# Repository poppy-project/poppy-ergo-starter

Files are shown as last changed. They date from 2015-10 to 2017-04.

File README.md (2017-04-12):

# Poppy Ergo Starter



Poppy Ergo Starter robot is a small and low cost 4-degree-of-freedom robot arm. It consists of very simple shapes which can be easily 3D printed with FDM printers and laser cutted.

It works with Dynamixel XL-320 motors, and a Raspberry Pi for control.

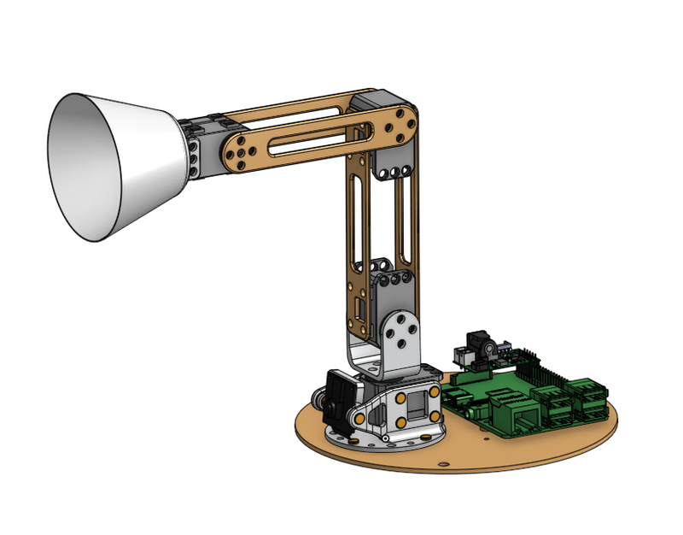
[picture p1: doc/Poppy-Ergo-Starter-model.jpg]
PoppyErgoStarter


It comes with three tools:
* a lampshade
* a grasper
* a pen holder

The Poppy Ergo Starter is ideal to start manipulating robots and learn robotic without difficulties.

It is particularly well suited for educational purposes (cheap, simple to assemble, and easily controllable) or can be a very nice desk decoration for geeks and makers...

## Contributing

You can share your experience, new design, ideas or questions on the [Poppy project forum](https://forum.poppy-project.org/).

To contribute to this repository, you can [fork it](https://help.github.com/articles/fork-a-repo/) and propose a [pull request](https://help.github.com/articles/using-pull-requests/) *([Another useful link](https://gun.io/blog/how-to-github-fork-branch-and-pull-request/))*

## License

All the technological development work made in the Poppy project is freely available under open source licenses. Only the name usage *"Poppy"* is restricted and protected as an international trademark, please contact us if you want to use it or have more information.

| License | Hardware | Software |
| --- | :---: | :---: |
| Title  | [Creative Commons BY-SA](http://creativecommons.org/licenses/by-sa/4.0/)  |[GPL v3](http://www.gnu.org/licenses/gpl.html)  |
| Logo  |   |GPL V3 (http://www.gnu.org/licenses/gpl.html)  |

## The Poppy project history

The Poppy project was born in 2012 in the [Flowers laboratory](https://flowers.inria.fr/) at [Inria Bordeaux Sud-Ouest](http://www.inria.fr/en/centre/bordeaux).
It was initiated during [Matthieu Lapeyre](https://github.com/matthieu-lapeyre)'s PhD Thesis surpervised by [Pierre Yves Oudeyer](http://www.pyoudeyer.com/). At the beginning, the development team was composed by [Matthieu Lapeyre](https://github.com/matthieu-lapeyre) (mechanics & design), [Pierre Rouanet](https://github.com/pierre-rouanet) (software) and [Jonathan Grizou](http://jgrizou.com/) (electronics).

This project is initially a fundamental research project financed by [ERC Grant Explorer](http://erc.europa.eu/) to explore the role of embodiement and morphology properties on cognition and especially on the learning of sensori-motor tasks.

## More on the project

- [Website](https://www.poppy-project.org)
- [Forum](https://forum.poppy-project.org)
- [Youtube](https://www.youtube.com/channel/UC3iVGSr-vMgnFlIfPBH2p7Q)
- [Twitter](https://twitter.com/poppy_project)
- [Flickr](https://www.flickr.com/photos/poppy-project)
- [Vimeo](https://vimeo.com/poppyproject)
- [Thingiverse](http://www.thingiverse.com/poppy_project/)

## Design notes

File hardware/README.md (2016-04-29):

## Onshape version
The up to date hardware version is made with [Onshape](https://www.onshape.com/), which is a proprietary online CAD software, free to use for public projects.

You can view and modify the hardware parts on Onshape ([link of the onshape project](https://cad.onshape.com/documents/57024ba6e4b0bd431e251b54/v/f9f9475a8e982b501b19085f/e/ed40471c06b378f3c094c206)), but an account (free) is required.

## OpenScad version
Poppy Ergo Starter was originally made by Jonathan Grizou (@jgrizou) with [OpenScad](http://www.openscad.org/).
This was inspired by the [Metabot project](https://github.com/Rhoban/Metabot/).

The OpenScad version of hardware is kept [here](https://github.com/poppy-project/poppy-ergo-starter/tree/OpenSCAD) for memory and educational example of an OpenScad project, but it is __no longer maintained__.

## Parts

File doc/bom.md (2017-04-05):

# Bill of materials

Here you will find the complete list of material (BOM) needed to build a Poppy Ergo Starter.

## Poppy's material

- 1x [Pixl board](https://github.com/poppy-project/pixl) *(electronic board to control XL320 motors)*
- 1x [disk_support.stl](https://github.com/poppy-project/poppy-ergo-starter/blob/master/hardware/STL/disk_support.stl) (using laser cutting) the 2D plan can be found [here](https://github.com/poppy-project/poppy-ergo-starter/tree/master/hardware/disk_support). *You can also 3D print the base but it will take a lot of time*
- 2x [4dof-parts](https://github.com/poppy-project/poppy-ergo-starter/tree/master/hardware/4dof-parts.pdf) by laser cutting
- the 3D printed parts [STL here](https://github.com/poppy-project/poppy-ergo-starter/tree/master/hardware/STL)
  - 1x [base.stl](https://github.com/poppy-project/poppy-ergo-starter/blob/master/hardware/STL/base.stl)
  - 1x [long_U.stl](https://github.com/poppy-project/poppy-ergo-starter/blob/master/hardware/STL/long_U.stl)
  - 1x [short_U.stl](https://github.com/poppy-project/poppy-ergo-starter/blob/master/hardware/STL/short_U.stl)
  - 1x [support_camera.stl](https://github.com/poppy-project/poppy-ergo-starter/blob/master/hardware/STL/long_U.stl)
  - the different tools
    - 1x [lamp.stl](https://github.com/poppy-project/poppy-ergo-starter/blob/master/hardware/STL/tools/lamp.stl)
    - 1x [gripper-fixation.stl](https://github.com/poppy-project/poppy-ergo-starter/blob/master/hardware/STL/tools/gripper-fixation.stl)
    - 1x [gripper-fixed_part.stl](https://github.com/poppy-project/poppy-ergo-starter/blob/master/hardware/STL/tools/gripper-fixed_part.stl)
    - 1x [gripper-rotative_part.stl](https://github.com/poppy-project/poppy-ergo-starter/blob/master/hardware/STL/tools/gripper-rotative_part.stl)
    - 1x [pen-holder.stl](https://github.com/poppy-project/poppy-ergo-starter/blob/master/hardware/STL/tools/pen-holder.stl)
    - 1x [pen-screw.stl](https://github.com/poppy-project/poppy-ergo-starter/blob/master/hardware/STL/tools/pen-screw.stl)

## Robotis parts

- 4x Robotis dynamixel motors XL-320
- 1x set of OLLO rivets (about 50 colored and 1 grey)
- 1x OLLO TOOL

## Screw

- 4x M2.5x6mm screw (for fixing the Raspberry Pi on the base)
- 4x M2x5mm screw (for fixing the camera)
- 4x M2 nuts (fixing camera)
- 1x Standoff Male/Female M2.5 10mm

## Various electronics

- 1x Raspberry Pi 2 or Raspberry Pi 3
- 1x micro SD 8Go
- 1x Rasperry Pi camera
- 1x AC power 7.5V 2A with a 2.1 x 5.5 x 9.5 jack connector ([this one](http://fr.rs-online.com/web/p/alimentations-enfichables/7262814/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) for instance).
- Short ethernet cable

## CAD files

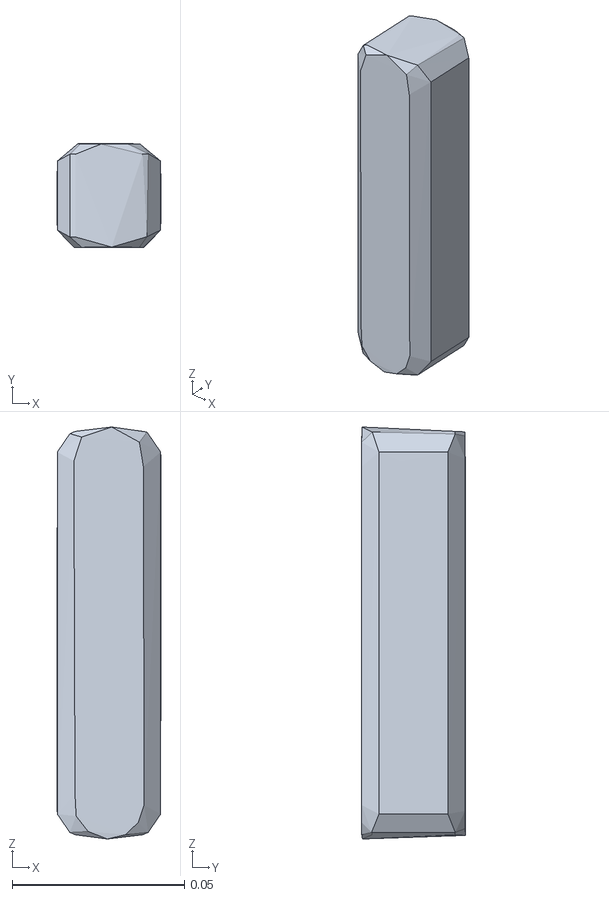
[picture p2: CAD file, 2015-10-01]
hardware/URDF/meshes/arm1_respondable.stl
0.0301 x 0.0301 x 0.119

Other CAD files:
hardware/STEP/tools/pen_holder.step
hardware/STEP/U_parts.step
hardware/STL/support_camera.stl
hardware/STL/tools/gripper-rotative_part.stl
hardware/URDF/meshes/base_motor_respondable.stl
hardware/STEP/base.step
hardware/STEP/tools/lamp.step
hardware/STL/4dofs-side2side.stl
hardware/STL/tools/gripper-fixation.stl
hardware/URDF/meshes/holder_visual.stl
hardware/STEP/tools/gripper.step
hardware/STL/short_U.stl
hardware/STL/tools/gripper-fixed_part.stl
hardware/URDF/meshes/holder_respondable.stl
hardware/STL/long_U.stl
hardware/URDF/meshes/base_motor_visual.stl
hardware/STL/4dofs-horn2horn.stl
hardware/STL/base.stl
hardware/STL/disk_support.stl
hardware/STL/tools/lamp.stl
hardware/STL/tools/pen-holder.stl
hardware/STL/tools/pen-screw.stl
hardware/URDF/meshes/U_horn_respondable.stl
hardware/URDF/meshes/U_horn_visual.stl
hardware/URDF/meshes/arm1_visual.stl
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

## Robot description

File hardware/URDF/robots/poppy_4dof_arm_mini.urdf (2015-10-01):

<?xml version="1.0" encoding="utf-8"?>
<robot name="Poppy_4dof_Arm_Mini">
	<link name="base_motor">
		<inertial>
			<origin xyz="0 -0.003349 -0.007144" rpy="0 0 0"></origin>
			<mass value="0.0391346684"></mass>
			<inertia ixx="0.01991511" ixy="-1.627E-12" ixz="-3.3502E-11" iyy="0.018856556" iyz="0.0010117547" izz="0.032481808"></inertia>
		</inertial>
		<visual>
			<origin xyz="0 0 0" rpy="0 0 0"></origin>
			<geometry>
				<mesh filename="package://meshes/base_motor_visual.STL"></mesh>
			</geometry>
			<material name="">
				<color rgba="0.9 0.9 0.9 1.0"></color>
			</material>
		</visual>
		<collision>
			<origin xyz="0 0 0" rpy="0 0 0"></origin>
			<geometry>
				<mesh filename="package://meshes/base_motor_respondable.STL"></mesh>
			</geometry>
		</collision>
		<mass>0.0391346684</mass>
	</link>
	<link name="U_horn">
		<inertial>
			<origin xyz="0 0.013288 0" rpy="0 0 0"></origin>
			<mass value="0.0042280066"></mass>
			<inertia ixx="0.0014620794" ixy="0" ixz="-8.78E-13" iyy="0.0011395926" iyz="0" izz="0.0006457789"></inertia>
		</inertial>
		<visual>
			<origin xyz="0 0 0" rpy="0 0 0"></origin>
			<geometry>
				<mesh filename="package://meshes/U_horn_visual.STL"></mesh>
			</geometry>
			<material name="">
				<color rgba="0.9 0.9 0.9 1.0"></color>
			</material>
		</visual>
		<collision>
			<origin xyz="0 0 0" rpy="0 0 0"></origin>
			<geometry>
				<mesh filename="package://meshes/U_horn_respondable.STL"></mesh>
			</geometry>
		</collision>
		<mass>0.0042280066</mass>
	</link>
	<link name="arm_1">
		<inertial>
			<origin xyz="0 0.000057479 0.049499928" rpy="0 0 0"></origin>
			<mass value="0.0430952766"></mass>
			<inertia ixx="0.08214364" ixy="2.97266E-10" ixz="5.81285E-10" iyy="0.083140664" iyz="-6.131977E-09" izz="0.0061720795"></inertia>
		</inertial>
		<visual>
			<origin xyz="0 0 0" rpy="1.5708 0 0"></origin>
			<geometry>
				<mesh filename="package://meshes/arm1_visual.STL"></mesh>
			</geometry>
			<material name="">
				<color rgba="0.9 0.9 0.9 1.0"></color>
			</material>
		</visual>
		<collision>
			<origin xyz="0 0 0" rpy="1.5708 0 0"></origin>
			<geometry>
				<mesh filename="package://meshes/arm1_respondable.STL"></mesh>
			</geometry>
		</collision>
		<mass>0.0430952766</mass>
	</link>
	<link name="arm_2">
		<inertial>
			<origin xyz="0 0.050999855 0" rpy="0 0 0"></origin>
			<mass value="0.010259289"></mass>
			<inertia ixx="0.014484899" ixy="0" ixz="-2.42E-13" iyy="0.004054289" iyz="1.06451E-10" izz="0.017657572"></inertia>
		</inertial>
		<visual>
			<origin xyz="0 0 0" rpy="0 1.5708 3.14160 "></origin>
			<geometry>
				<mesh filename="package://meshes/arm2_visual.STL"></mesh>
			</geometry>
			<material name="">
				<color rgba="0.9 0.9 0.9 1.0"></color>
			</material>
		</visual>
		<collision>
			<origin xyz="0 0 0" rpy="0 1.57080 3.14160"></origin>
			<geometry>
				<mesh filename="package://meshes/arm2_respondable.STL"></mesh>
			</geometry>
		</collision>
		<mass>0.010259289</mass>
	</link>
	<link name="holder">
		<inertial>
			<origin xyz="0 -0.012510048 -0.000058315" rpy="0 0 0"></origin>
			<mass value="0.0212559855"></mass>
			<inertia ixx="0.0063271895" ixy="-1.9672E-11" ixz="-1.6458E-11" iyy="0.0024594695" iyz="1.7191568359E-05" izz="0.0058998525"></inertia>
		</inertial>
		<visual>
			<origin xyz="0 0 0" rpy="0 0 0 "></origin>
			<geometry>
				<mesh filename="package://meshes/holder_visual.STL"></mesh>
			</geometry>
			<material name="">
				<color rgba="0.9 0.9 0.9 1.0"></color>
			</material>
		</visual>
		<collision>
			<origin xyz="0 0 0" rpy="0 0 0"></origin>
			<geometry>
				<mesh filename="package://meshes/holder_respondable.STL"></mesh>
			</geometry>
		</collision>
		<mass>0.0212559855</mass>
	</link>
	<joint name="M1" type="revolute">
		<origin xyz="0 0 0.04" rpy="-1.5708 0 0"></origin>
		<parent link="base_motor"></parent>
		<child link="U_horn"></child>
		<axis xyz="0 1 0"></axis>
		<limit lower="-2.617993875" upper="2.617993875" effort="3.1" velocity="7.0"></limit>
	</joint>
	<joint name="M2" type="revolute">
		<origin xyz="0 0 0" rpy="0 0 0"></origin>
		<parent link="U_horn"></parent>
		<child link="arm_1"></child>
		<axis xyz="0 0 1"></axis>
		<limit lower="-1.5708" upper="1.5708" effort="3.1" velocity="7.0"></limit>
	</joint>
	<joint name="M3" type="revolute">
		<origin xyz="0 -0.099 0" rpy="0 0 0"></origin>
		<parent link="arm_1"></parent>
		<child link="arm_2"></child>
		<axis xyz="0 0 1"></axis>
		<limit lower="-2.617993875" upper="2.617993875" effort="3.1" velocity="7.0"></limit>
	</joint>
	<joint name="M4" type="revolute">
		<origin xyz="0 -0.099 0" rpy="0 0 0"></origin>
		<parent link="arm_2"></parent>
		<child link="holder"></child>
		<axis xyz="0 0 0"></axis>
		<limit lower="-2.617993875" upper="2.617993875" effort="3.1" velocity="7.0"></limit>
	</joint>
</robot>

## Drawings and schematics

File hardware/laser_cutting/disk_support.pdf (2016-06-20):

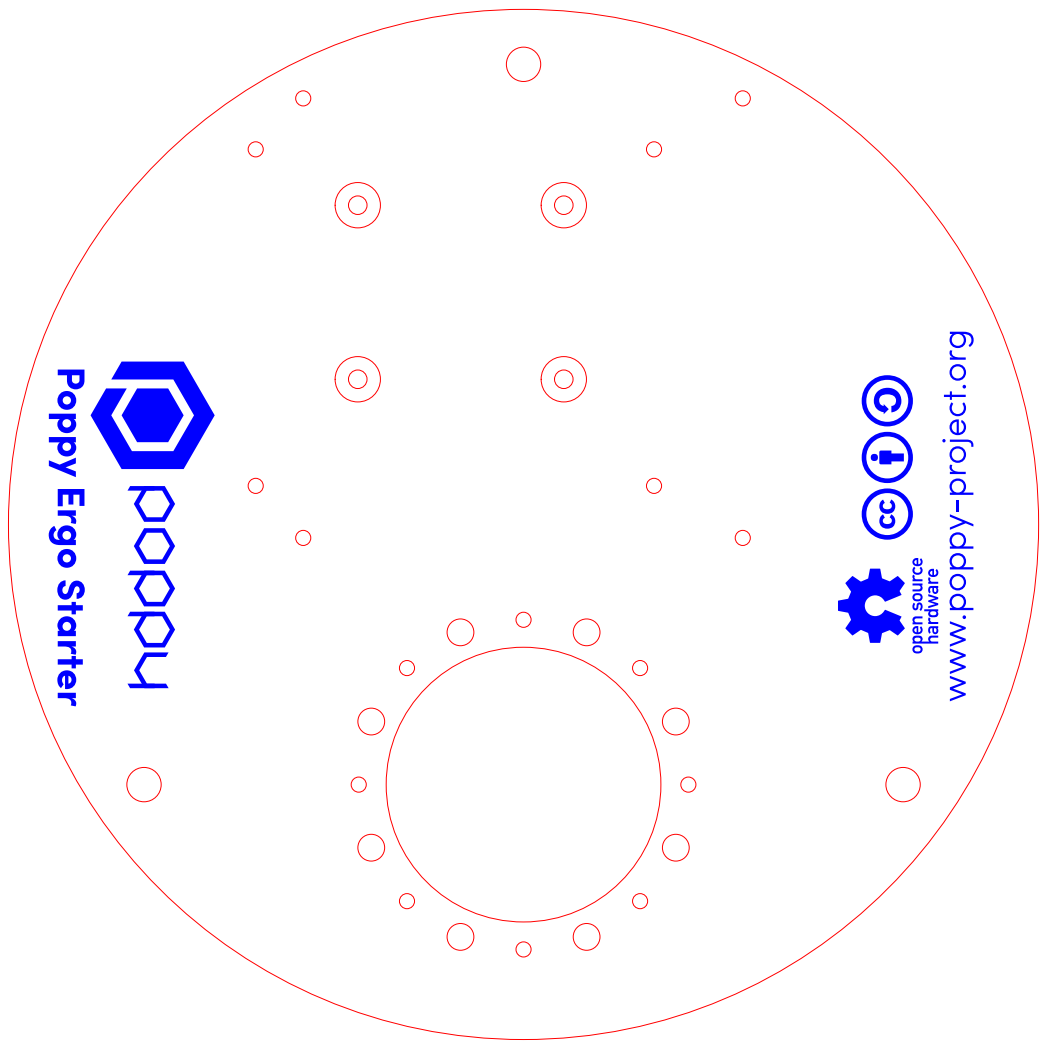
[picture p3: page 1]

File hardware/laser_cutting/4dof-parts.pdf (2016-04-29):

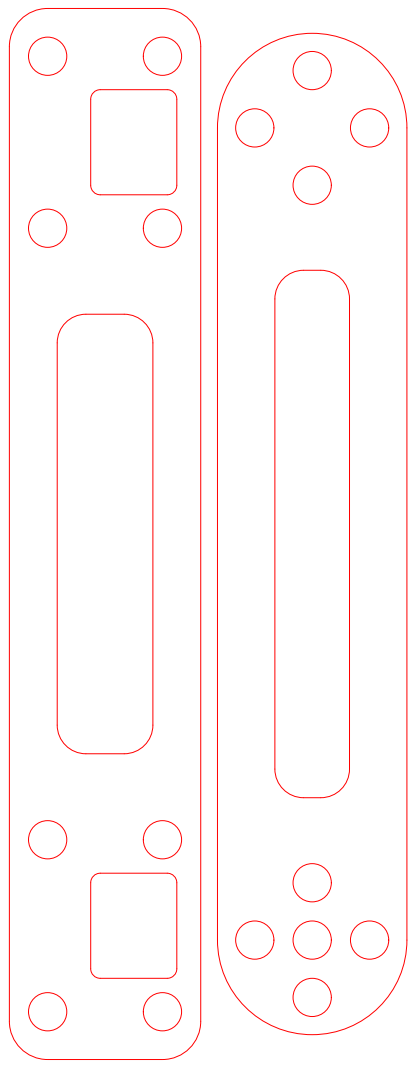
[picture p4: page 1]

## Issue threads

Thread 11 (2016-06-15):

Laser cutting

jjehl, 2016-06-15:
Cuttings for brace are missing in the pdf file.
It could be better to put diameter hole to 4 mm and not 4.1 because the laser has 0.2mm wide (to much clearance).

How did you process to make the PDF file for laser cutting from the onshape drawing ? I can update the doc. with the cutting for the brace.

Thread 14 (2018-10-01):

Usage with Snap!

celbertin, 2018-10-01:
Hi! I just installed Poppy Ergo Starter using:

> curl -L https://raw.githubusercontent.com/poppy-project/raspoppy/master/raspoppyfication.sh | bash -s "poppy-ergo-starter"

I can use Poppy with Jupyter, but I can't move it using Snap! I can only get the motor list, get current position, and change LED colors, but I can't move the motors.

How can I use Poppy with Snap?

show0k, 2018-10-02:
Hi,
Did you put the robot in stiff mode ?

celbertin, 2018-10-02:
Hi!
I did put it in stiff mode. I notice the problem is related to moving the robot with Jupyter and then trying to move it using it with Snap. Snap works fine if I don't move the robot using Jupyter.

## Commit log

2015-04-17 updated all pathes
    [U_horn_to_horn.scad, base.scad, base_frame.scad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]
2015-04-17 ignoring stl files
2015-05-04 circular base out of robot module
    [poppy_4dof_arm_mini.scad]
2015-05-04 updated read with STL view
2015-05-06 changing default param
    [pen_holder_frame.scad, poppy_4dof_arm_mini_def.scad]
2015-05-09 specific frames are now in robots-scad
    [base_frame.scad, pen_holder_frame.scad, poppy_4dof_arm_mini.scad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]
2015-05-09 modified generation of parts for new specific frame location
    [base.scad, pen_holder.scad]
2015-07-13 updated submodule for holes by defaults in side frame and circular base
2015-10-01 added v-rep scene
    [U_horn.stl, U_horn_respondable.stl, U_horn_visual.stl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]
2015-10-01 removed base meshes
    [U_horn.stl, arm1.stl, arm2.stl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]
2016-04-28 remove openSCAD model
    [U_horn_to_horn.scad, base.scad, horn_to_horn.scad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]
2016-04-28 activate Git LFS for STL and STEP files
2016-04-28 add STL for 3D printing parts
    [4dofs-horn2horn.stl, 4dofs-side2side.stl, base.stl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]
2016-04-28 add STEP parts of the robot
    [U_parts.step, base.step, gripper.step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]
2016-04-28 add vectoriel files for laser cutting
2016-04-28 add the pixl board as submodule
2016-04-28 add documentation for the BOM
2016-06-15 adding brace for laser cutting
2016-06-15 adding brace to laser cutting
2016-06-15 Revert "initial commit"
    This reverts commit d3a494849d16e6078d1524b642f4755f68912ed9.
    [arm2_respondable.stl, arm2_visual.stl, base_motor_respondable.stl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]
2016-06-15 weird changes
    [base_motor_respondable.stl, base_motor_visual.stl, holder_respondable.stl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]
2016-06-15 deleted file
    [base_motor_respondable.stl, base_motor_visual.stl, holder_respondable.stl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]
2017-04-05 Prepare code for pypot 3
    BOM and submodules were updated

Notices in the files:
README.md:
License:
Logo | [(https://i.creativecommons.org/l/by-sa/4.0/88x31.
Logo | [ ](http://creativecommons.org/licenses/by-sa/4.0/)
